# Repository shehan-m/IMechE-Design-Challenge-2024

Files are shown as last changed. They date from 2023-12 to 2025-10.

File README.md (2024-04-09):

# IMechE Design Challenge 2024

## Installation

OS: Raspberry Pi OS (Legacy, 32-bit) Lite

- **Step 1:** \
  To download code, it is necessary to have git installed:

```shell
sudo apt-get update && sudo apt-get install git -y
```

- **Step 2:** \
  Now install prerequisites for firmware:

```shell
sudo apt-get install python3-opencv && sudo apt-get install fswebcam
```

- **Step 3:** \
  Once these are installed, use the following command to clone the repo into the home directory:

```shell
cd ~ && git clone https://github.com/shehan-m/IMechE-Design-Challenge-2024/
```

## How to run code on startup

- **Step 1:** \
  Open the `rc.local` file using nano editor:

```shell
cd ~ && sudo nano /etc/rc.local
```

- **Step 2:** \
  Make bash script executable:

```shell
sudo chmod +x /IMechE-Design-Challenge-2024/Firmware/startup.sh
```

- **Step 3:** \
  Add the following commands above `exit 0`

```shell
sudo apt-get update && sudo apt-get install git -y
```

## Electronics

### Wiring Diagram
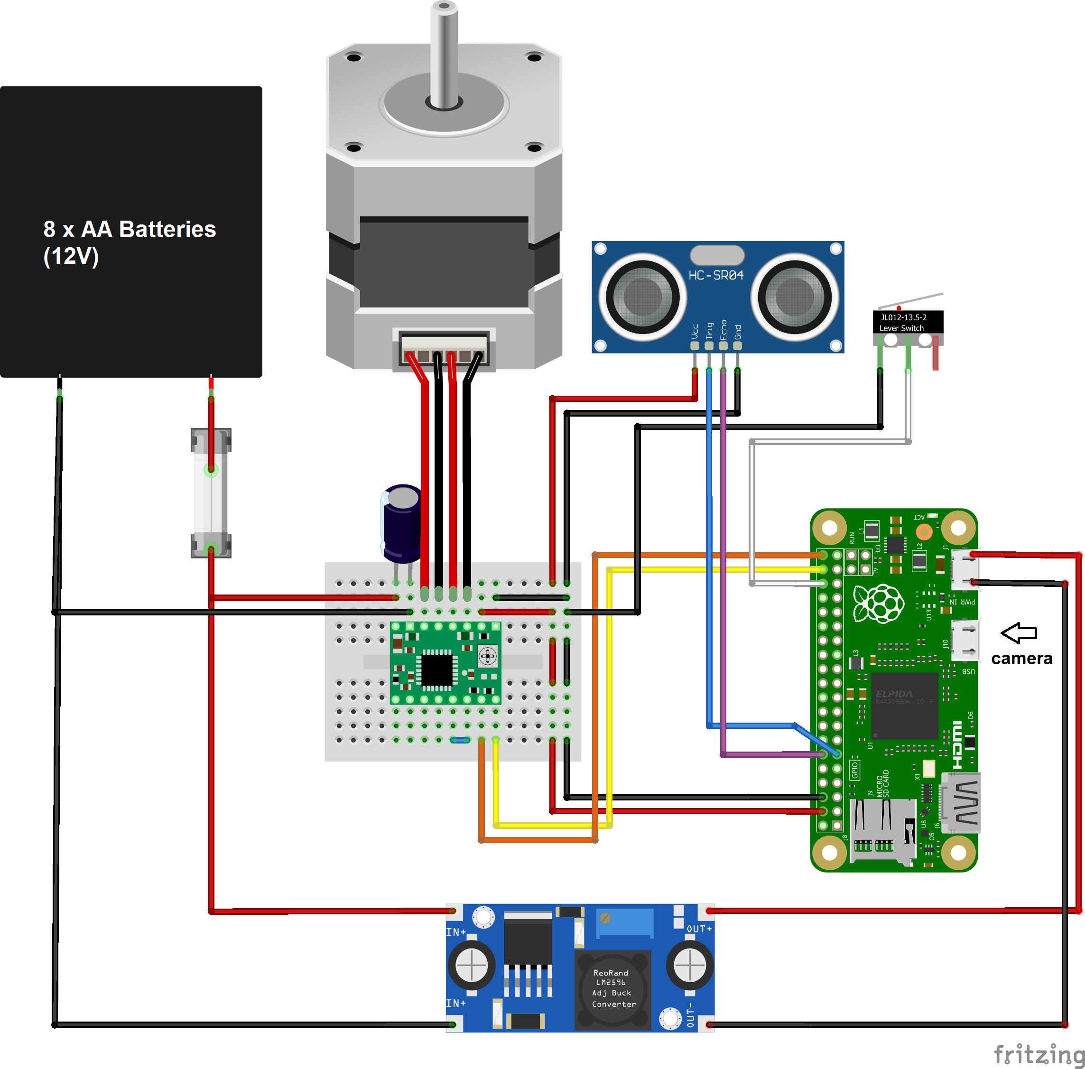
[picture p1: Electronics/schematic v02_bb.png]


### Limit switch

switch type: SPDT

#### This switch has three terminals:

- Common (COM): The common terminal
- Normally Open (NO): Connected to COM when the switch is pressed
- Normally Closed (NC): Connected to COM when the switch is not pressed

### Stepper driver current limiting

Vref = Imax * 8 * Rs

where, Imax is the current limit of the stepper motor, Rs is the resistance of the current sensing resistor (R5 on driver board)

In our case, Imax is 350 mA and Rs is 0.1 Ohms. Let's run the stepper motor at 60% of its rating. From this we get Vref:

Vref = (0.350 * 0.6) * 8 * 0.1 = 0.17 V

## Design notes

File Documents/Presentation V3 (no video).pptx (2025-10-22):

## IMechE Design Challenge 2024

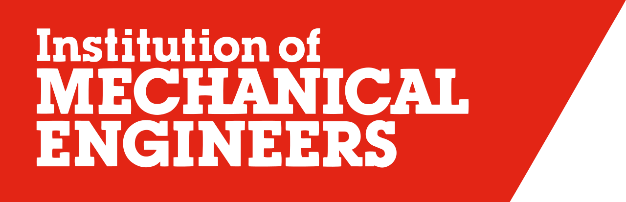
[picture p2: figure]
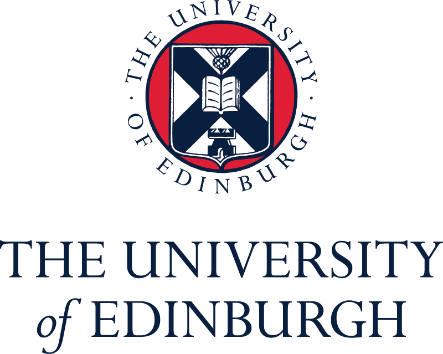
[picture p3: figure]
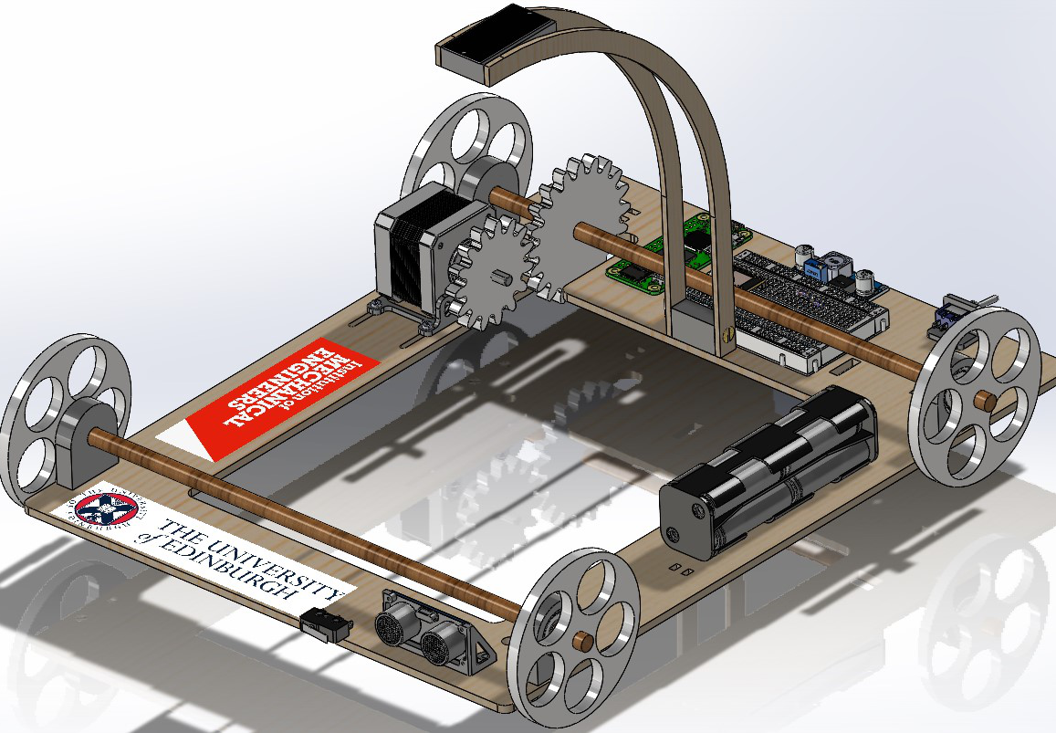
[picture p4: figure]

Gursager Singh
Shehan Medagedara
Harry Wang

## Challenge Overview

Advanced Category:
- Usage of Computer Vision
- Using motor and gear reduction for accurate movement

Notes: Went with Advanced category -> gave us the opportunity to use computer vision to detect the target, as well as use a motor in conjunction with gear reduction system to ensure accurate movement

## Vehicle Design

## Design Overview

NEMA 17 Stepper Motor

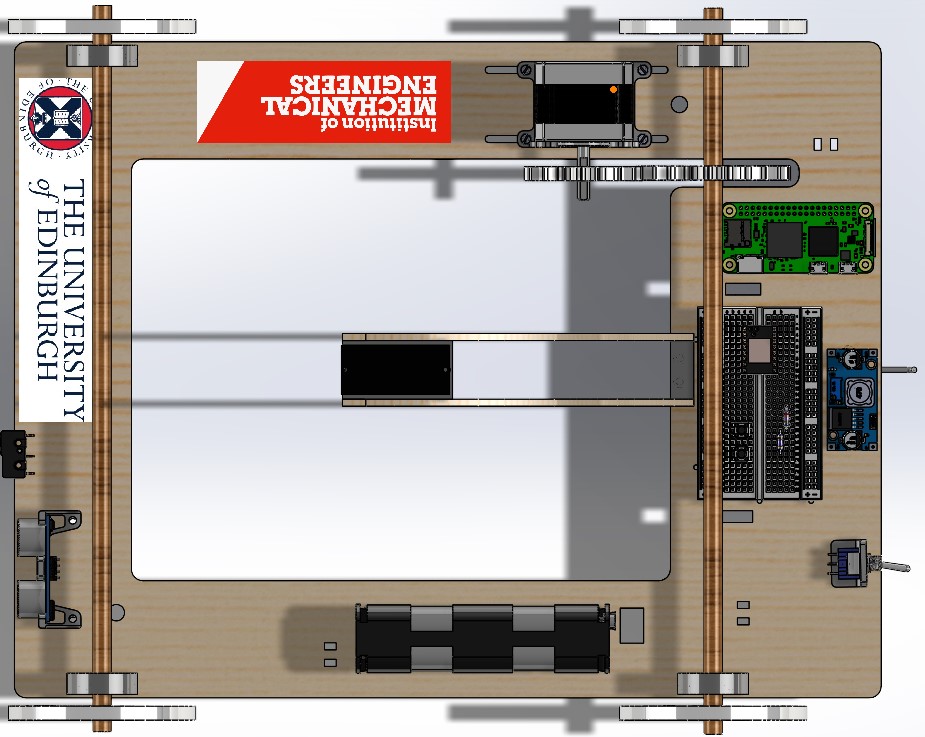
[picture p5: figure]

Wheel

Axle Holder + Ball bearings

Axle

Motor Gear

Raspberry Pi Zero 2 W

Breadboard

Output Gear

Limit Switch

TMC2208 V3 Stepper Driver

Buck Converter

Webcam

Ultrasonic Sensor (HC-SR04)

Battery Pack

On/Off Switch

## Chassis

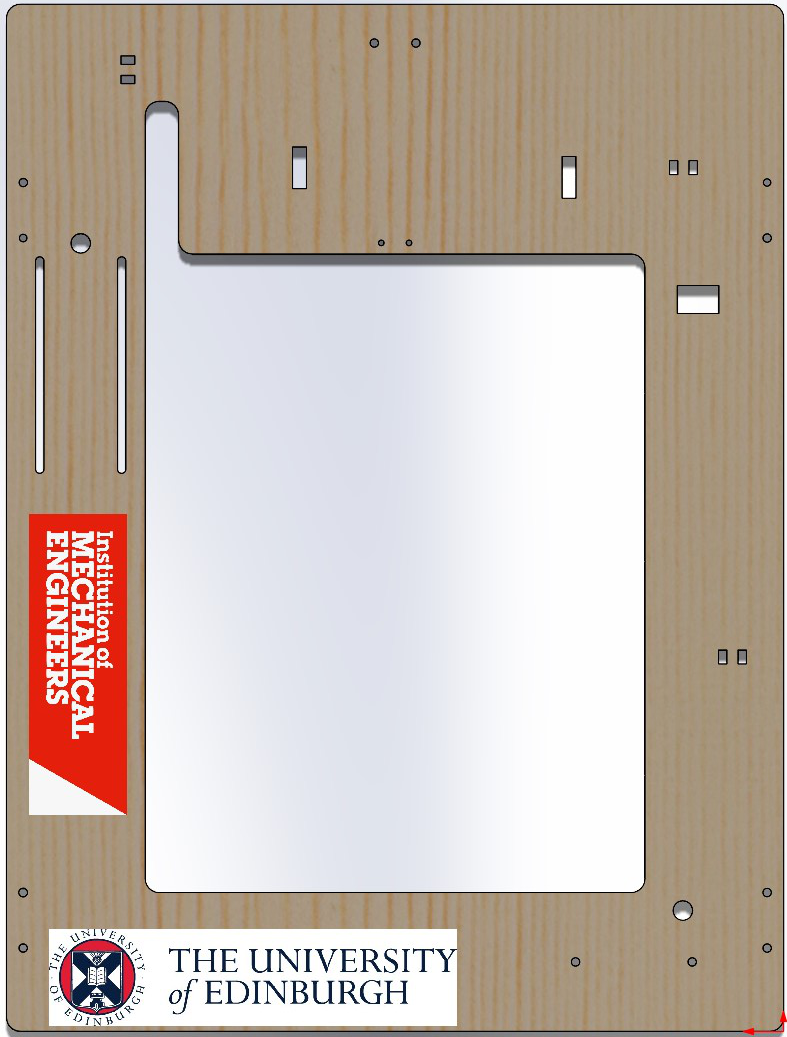
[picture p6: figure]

- 0.4mm MDF
- Target detection gap
- Drill holes to securing components
- Cable routing channels

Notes: 0.4mm MDF: perfect thickness and material to withstand weight and forces while staying relatively cheap
Large gap in centre for optimal target detection, system works best when target is directly underneath camera
Cable routing: ensures that the system looks neat, keeps cables out of the way. Dangling cables = hazard

## Powertrain

- NEMA 17 Motor
- Reduction gears at 4:3 reduction ratio
- Angular velocity of wheel = 0.75 of that of motor
- Allows stable movement

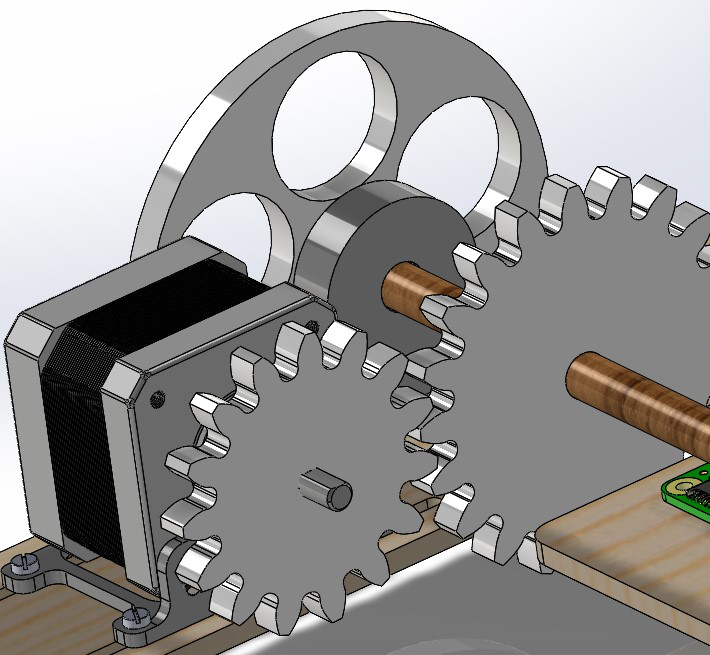
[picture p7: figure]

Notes: The NEMA 17 motor was chosen to deliver the power required

Motor needed to run at a certain angular velocity or else it will stutter. Reduction ratio allows the motor to run at higher speed while wheel travels slower and more accurately

## Target Detection Method

Initial idea: use a colour sensor with an Arduino
Problem: boundary between different colours could not be identified precisely
Solution: computer vision
= using an algorithm to detect circles from camera input

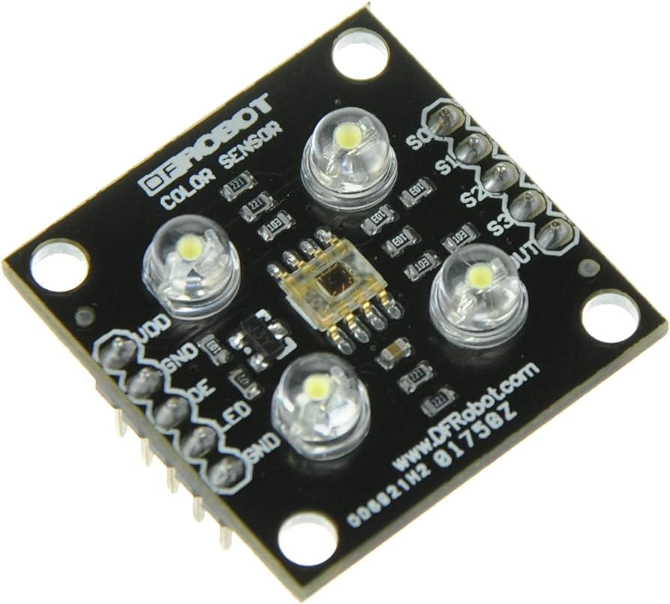
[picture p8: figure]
DFRobot SEN0101 TCS3200 Color Sensor/Color Detector : Amazon.ca: Tools & Home Improvement
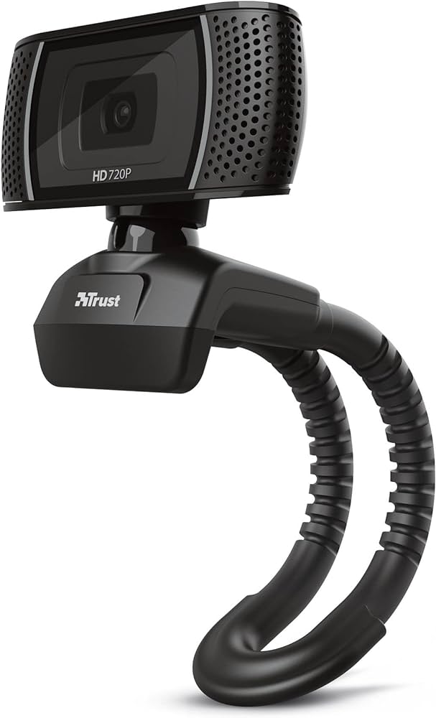
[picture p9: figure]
Trust Trino HD Webcam with Microphone, 1280x720, 30 FPS, Universal Stand, USB, Web Camera with Photo Button for Streaming, Video Calling, Skype, Teams, Zoom, PC, Computer, Laptop, Mac - Black : Amazon.co.uk:

## Circuit Diagram

Safety
- Power Switch
- Fuse
- Insulation on 12 V supply
Functionality
- Start button
- Reset button

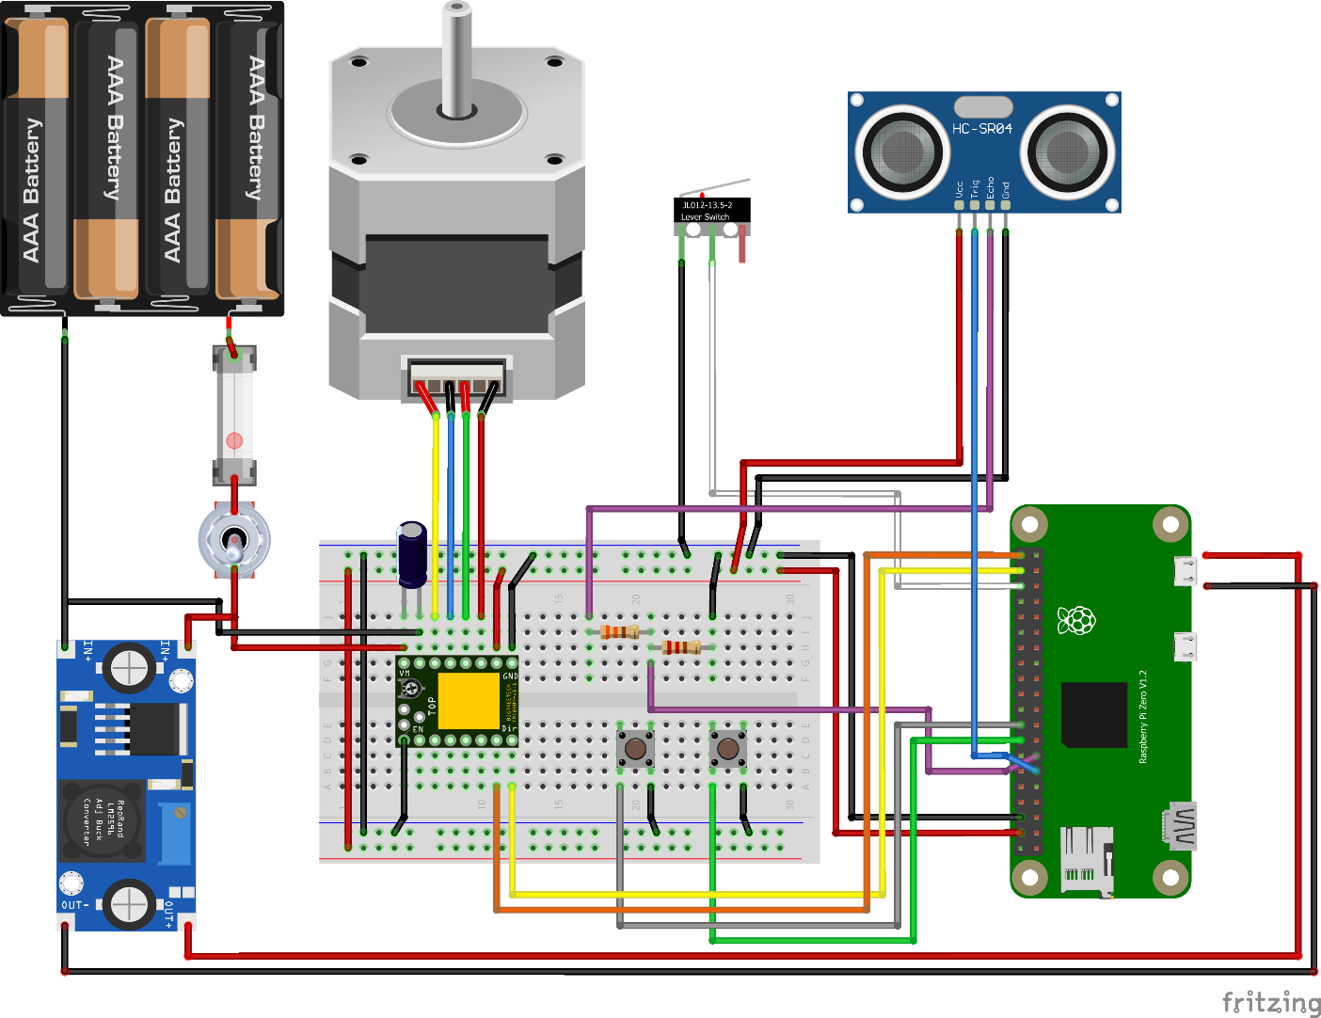
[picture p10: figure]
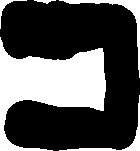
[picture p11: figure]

R2

12 V IN

R1

Camera In

5 V OUT

RESET Button

START Button

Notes: This circuit diagram outlines the essential components and connections for the device. Safety features include a power switch and a fuse to protect against electrical faults. A start and reset button can be used for easier control of the device.

## Power Distribution

Battery supply voltage:
- 12 V
Operating voltages:
- Stepper motor – 12 V
- Raspberry Pi – 5 V

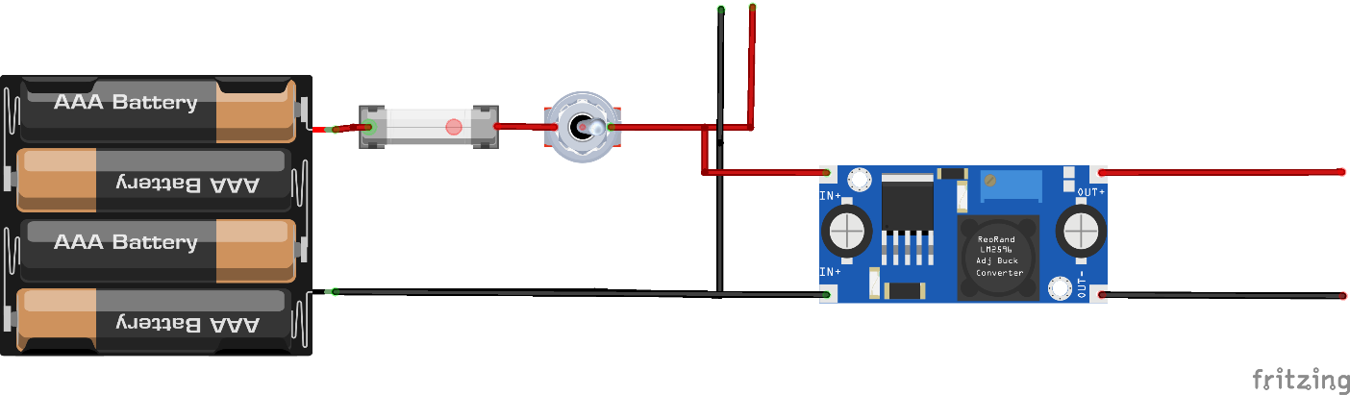
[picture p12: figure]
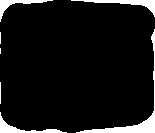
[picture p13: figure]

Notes: The whole system runs on a 12 V battery pack which has to power the Raspberry Pi and the stepper motor, both with different operating voltages. So, the supply voltage is split in parallel to the motor driver and to the buck converter. The buck converter steps down the battery voltage to 5 V which then supplies it to the Pi.

DO NOT READ:
- buck converter is a type of switch-mode power supply (SMPS) that changes voltage through duty cycle control.
- buck converter stabilises voltage - protect the Raspberry Pi against voltage fluctuations that could occur

## Calculating Vref

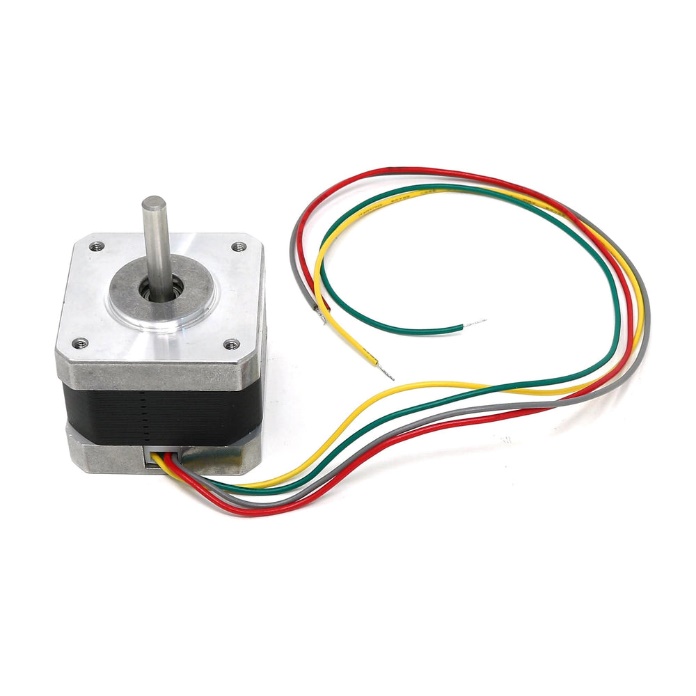
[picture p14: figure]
Stepper Motor - NEMA-17 size - 200 steps/rev, 12V 350mA - The Pi Hut

V_(ref) =I_(max) ∗8∗R_s
Where, I_(max) is the current limit of the stepper motor, R_s is the resistance of the current sensing resistor.
Motor Specification:
I_(max) = 350 mA
R_s = 0.1 Ω
V_(ref) =(0.350∗0.8)∗8∗0.1=0.22 V

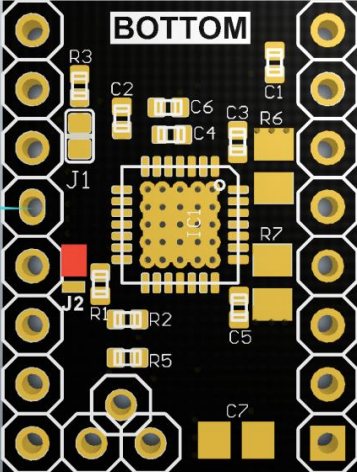
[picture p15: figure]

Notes:
The motor driver uses Vref to set the maximum amount of current that can flow through the motor coils. This needs to be calculate so not to damage the motor due to excessive current. For our case, Rs is the resistance of the R5 resistor on the driver board. From the motor specification we can get a Vref value of of 0.22 V. Also, to reduce heating in the motor, we’re operating it at 80% of its current limit.

## Protecting the Raspberry Pi

- General Purpose Input/Output (GPIO) pins on the Raspberry Pi operate at 3.3 V.
- Operating voltage of the ultrasonic sensor (HC-SR04) is 5 V.
- Thus, ultrasonic sensor input to Raspberry Pi must be lowered
V_(out) =(R1)/(R1+R2)∗V_(in) =330/(330+470) ∗5≈3.3 V
- Buck converter stabilises supply voltage.

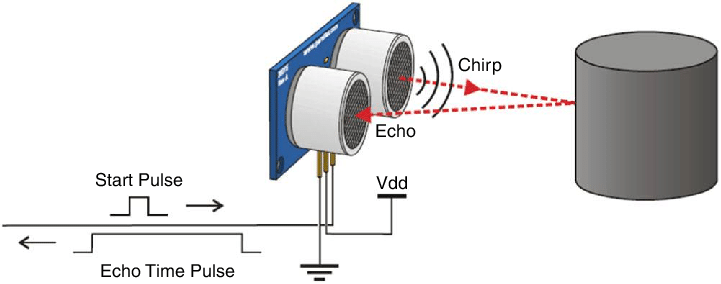
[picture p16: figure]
Working principle of ultrasonic sensor | Download Scientific Diagram

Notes: The GPIO pins on the Pi are designed to handle a maximum of 3.3 V. Exceeding this voltage can damage the Pi. This is a problem since the ultrasonic sensor operates at 5 V so, when the sensor sends an echo signal (indicating that it has detected an object) to the pi, the voltage level of this signal will be about 5 V. So, a potential divider is used to lower the echo signal voltage.

DO NOT READ: the echo signal is a series of HIGH & LOW (3.3V or 0 V) signals, so don’t have to save integrity of wave or anything like that

## Vehicle Operation

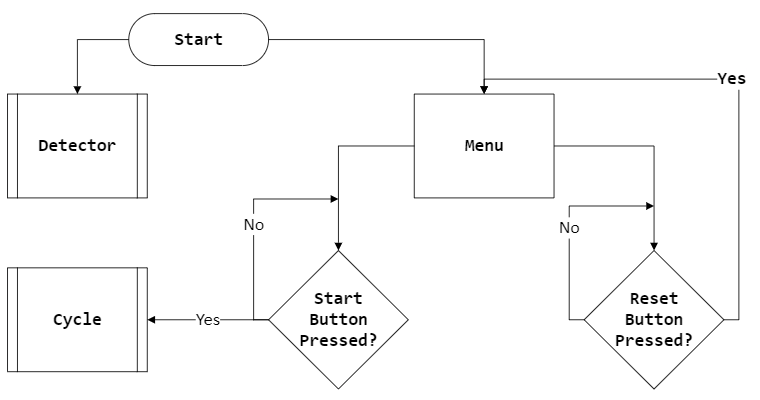
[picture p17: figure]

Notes: When the power switch is turned the the detector and a menu function starts. The menu continuously checks for button presses and starts the run/cycle if the start button is pressed, and reset the cycle if the reset is pressed. The detector starts at the same time as the menu because it takes time to boot up and vehicle doesn’t have to wait for that to happen.

## Vehicle Operation

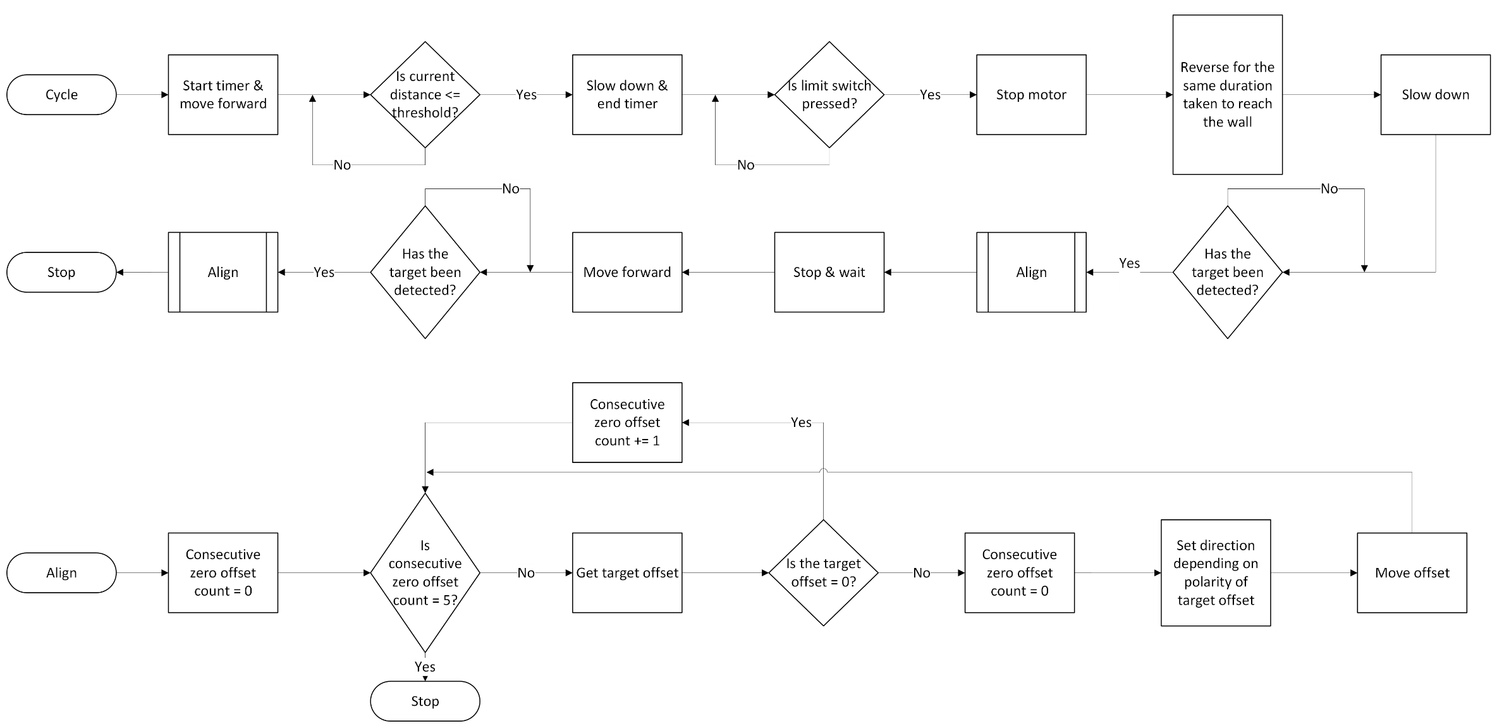
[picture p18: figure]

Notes:
Once the stat button has been pressed the vehicle moves towards the wall, continuously checking if the current distance to the wall is below a threshold value. If it is below the vehicle slows down and continues until the limit switch is pressed. Once this has been pressed the vehicle stops are reverse to the target and aligns itself. Once aligned, it waits and moves forward to the next target and aligns for a final time. The alignment process is very simple it moves motor by the offset given by the camera and does this until 5 offset readings return as 0 – meaning aligned.

Once the start button has been pressed the device begins to move forward & starts a timer. It continues to move forward until, the distance to the wall is less than a threshold value. Once at the threshold the device slows down, the timer is stopped and continues to move forward until the limit switch has been pressed. The motor stops & then reverses for the measured duration of time. After this time the device slows down and searches for the target. Once found it aligns itself & waits then moves forward to the second target and aligns again. The alignment process is very simple it moves the motor by offset given by the camera and does this until 5 offset readings return as 0 – meaning aligned.

## Detector – Computer Vision

Raw Input Video

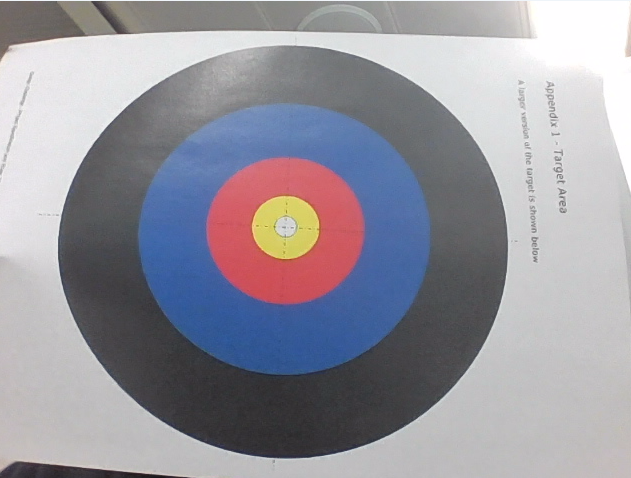
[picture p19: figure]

Colour Segmentation

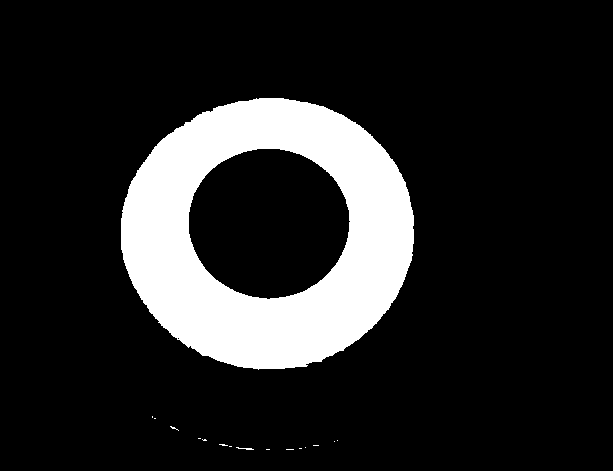
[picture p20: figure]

Mask Applied to Video

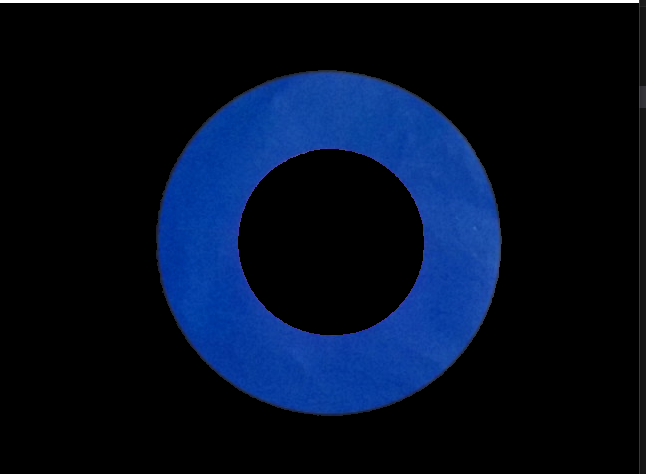
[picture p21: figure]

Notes: The input video feed is used to detect and isolate blue ring which can then be used to calculate the offset of its centre from the centre of the video.

To isolate the blue ring, a threshold is applied to select only the specified blue hues in the video. The white region represent where blue is detected.

This can then be used as a mask to get only the blue part of the input video.

## Detector – Computer Vision

Denoising

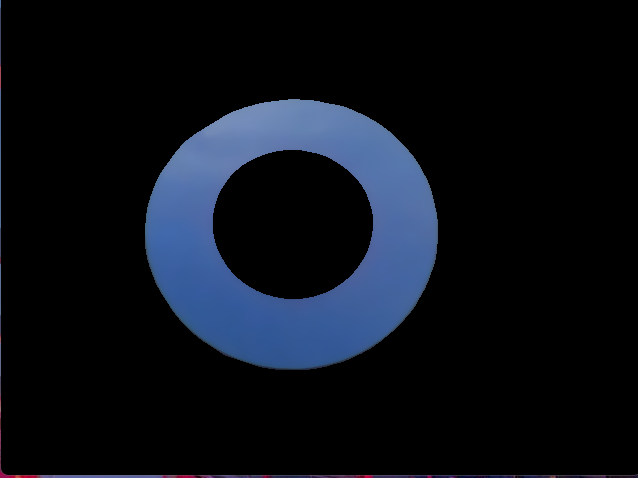
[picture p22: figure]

Greyscale Conversion

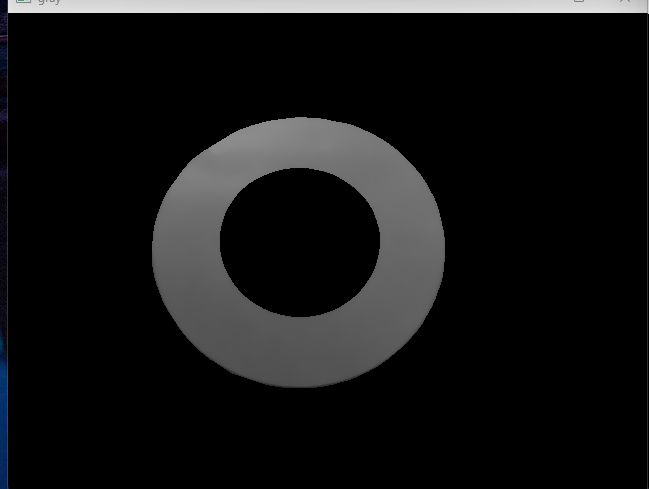
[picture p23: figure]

Contour Detection

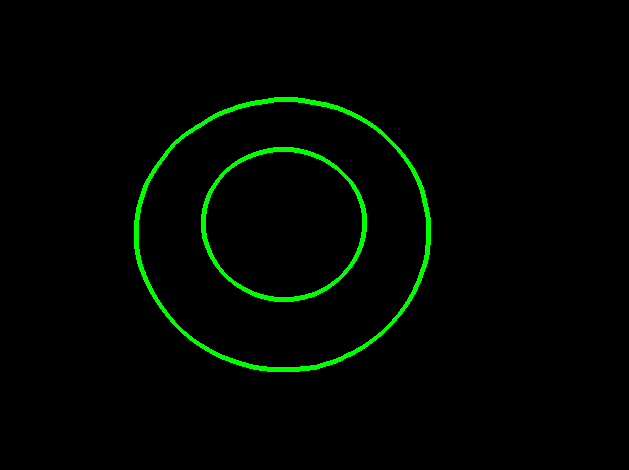
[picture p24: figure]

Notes: The produces a very noisy result which can affect the offset calculations. So, a median filter is applied to remove any noise.

Then converting the video to greyscale allows for easier and more accurate contour detection.

Finally, the contours are detected and are used to find the offset of the target from the centre of the video.

## Bill of Materials

## Overview

- Budget
- £80 excl. items less than 20p
- Total
- £79.25 excl. items less than 20p
- £82.96 incl. items more than 20p
- Remaining
- £0.75 from iMechE BoM

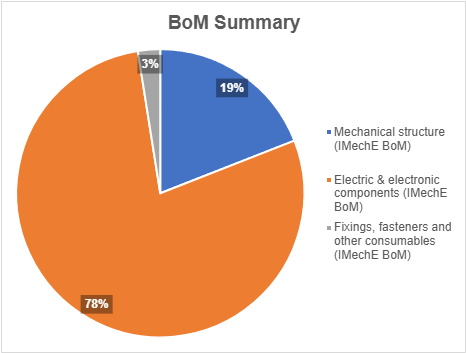
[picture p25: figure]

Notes: Note: do not simply just read off of the notes. Just say “here is the Bill of Materials overview” and state that we were under budget!

Pie chart shows for the iMechE BOM
Analyse from pie chart:
Focus on computer vision meant that more expenditure went towards electrical side
Mechanical components were quite cheap due to in-house facilities and smart usage of 3D printing and laser cutting

BOM shows well managed funding

## Thank you!

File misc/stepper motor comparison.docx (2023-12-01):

| NEMA 17 Stepper Motor | 28BYJ-48 Stepper Motor
Rated Voltage | 9-12 V | 5 V
Rated Current | 1.4 A
Step Angle | 0.9 degrees per step (micro stepping available) | 5.6 degrees per step
Torque | >= 0.127 Nm | >0.00343 Nm
Price | ~£10 | ~£8
Driver Included | No | Yes (ULN2003A)
Driver Price (if, not included) | ~£3-5 | N/A
Weight | 200 g | 33 g
Dimensions | 42.3 x 42.3 x 26.5 mm | 40 x 30 x 19 mm

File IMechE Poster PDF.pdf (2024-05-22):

## Target Detection

## Device Operation

## Bill of Materials

# IMechE Design Challenge 2024

Gursager Singh, Shehan Medagedara, Harry Wang

## Structure

Usage of iterative design and testing process
Laser cut MDF base structure for best support
Gap in centre of base to ensure best visual on target at a direct angle
Motor run through a 4:3 reduction gear system to ensure smooth and stable movement Cable-routing channels to ensure neat presentation

IMechE BoM Total: £73.07
Comprehensive Total: £77.00 Excess Funds: £6.93

Video feed is processed to highlight specific the colour of interest to act as a mask. In this case, blue. The mask is applied to the input video.

Noise is removed from the masked video by applying a median filter. Then, converted to greyscale for easier contour detection. The Centre of the target is determined from the centre of largest contour.

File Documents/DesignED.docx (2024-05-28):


DesignED

Gursager Singh

Shehan Medagedara

Harry Wang

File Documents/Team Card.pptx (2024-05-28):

## DesignED


Gursager Singh Hardeep Singh
Shehan Medagedara
Harry Wang

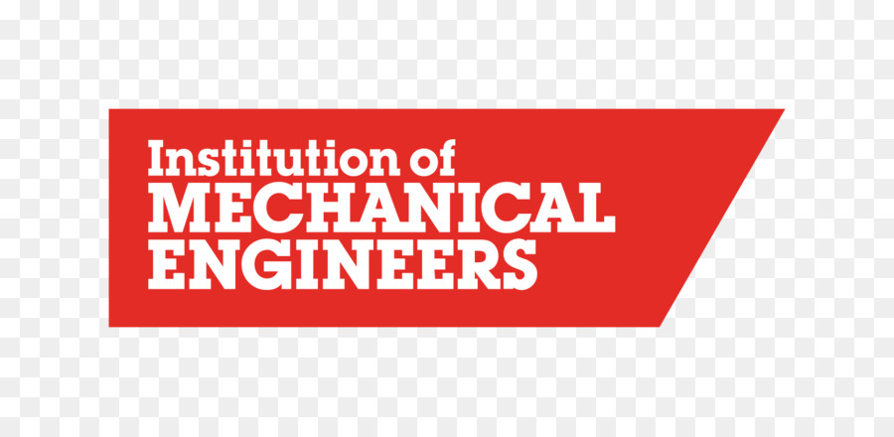
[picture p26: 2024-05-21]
Pictures/kisspng-institution-of-mechanical-engineers-mechanical-eng-mechanical-engine.jpg

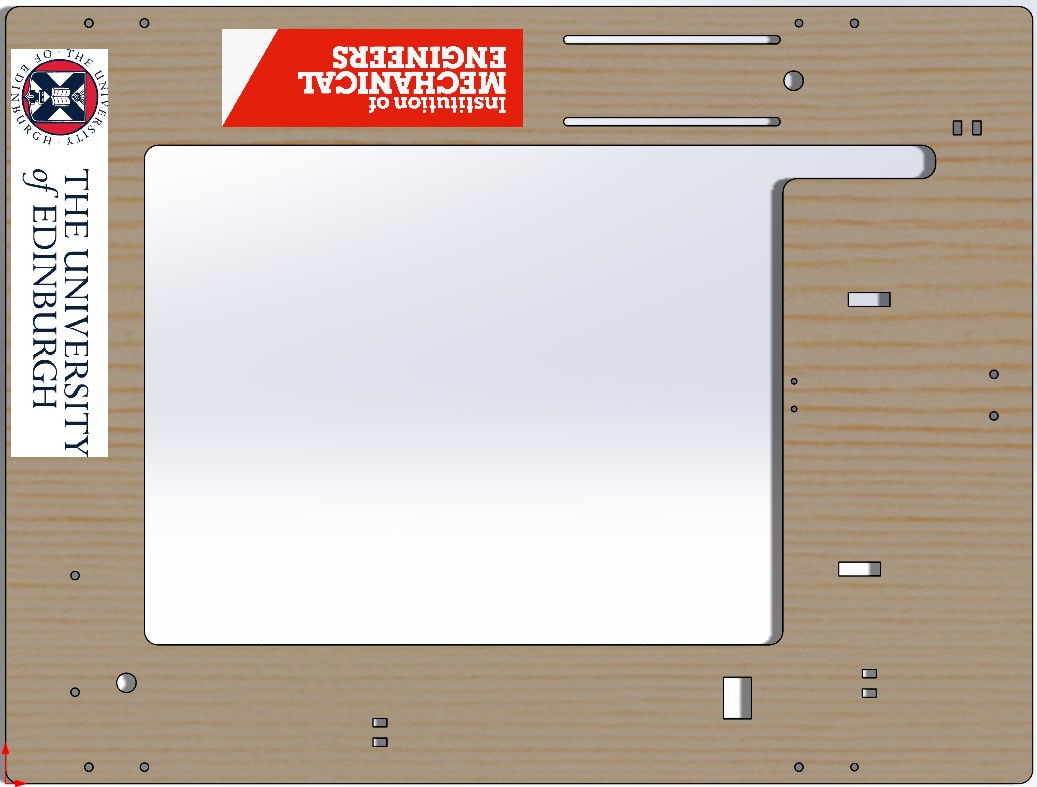
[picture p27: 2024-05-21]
Pictures/Chassis.jpg

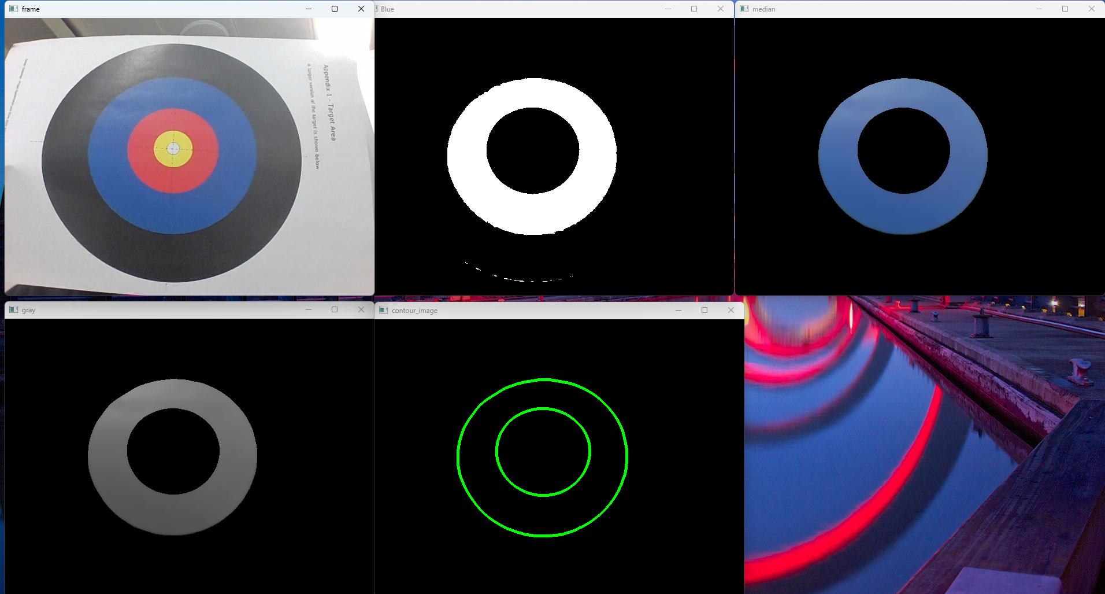
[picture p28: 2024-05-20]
Electronics/Screenshot 2024-05-20 135401.png

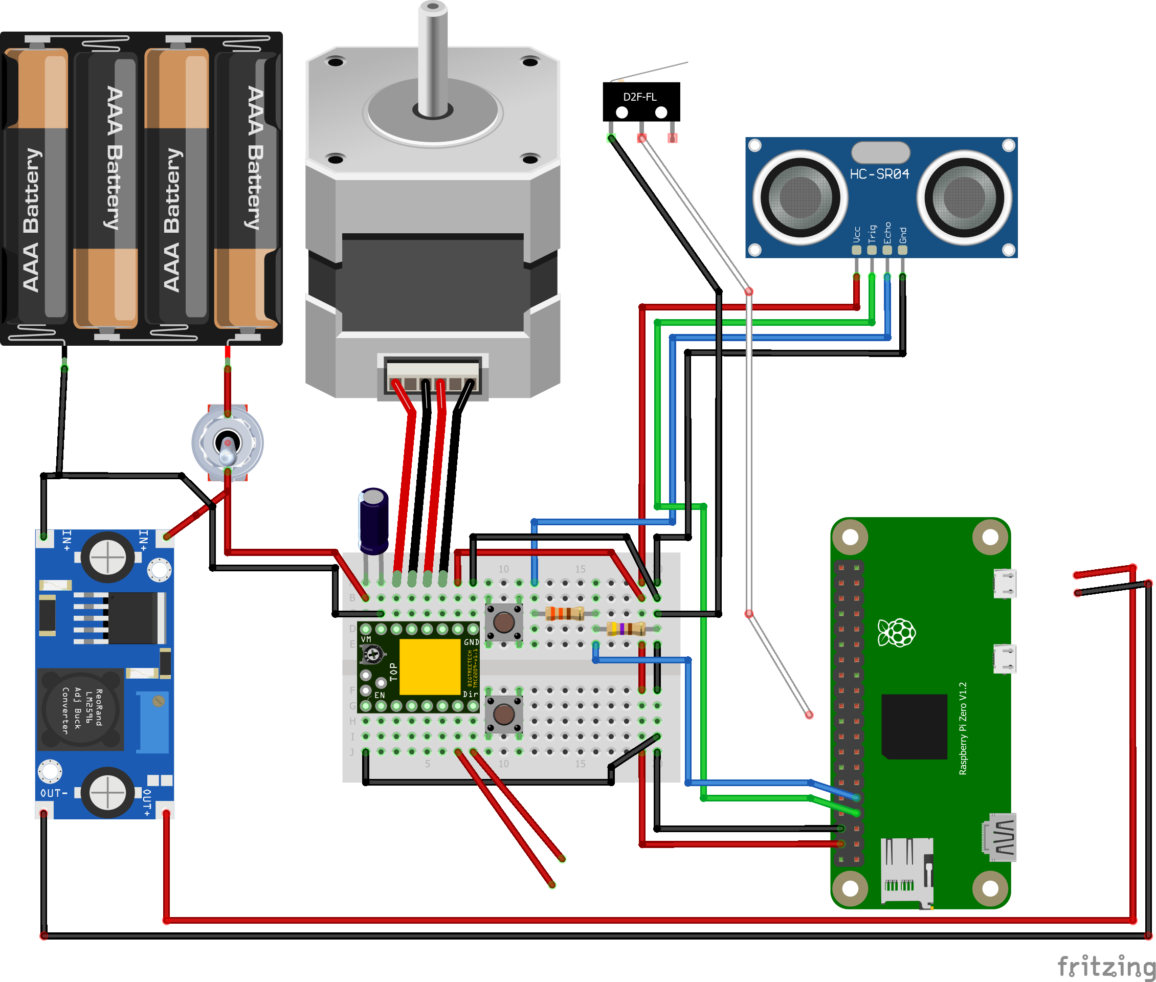
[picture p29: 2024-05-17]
Electronics/circuit diagram v03_bb.png

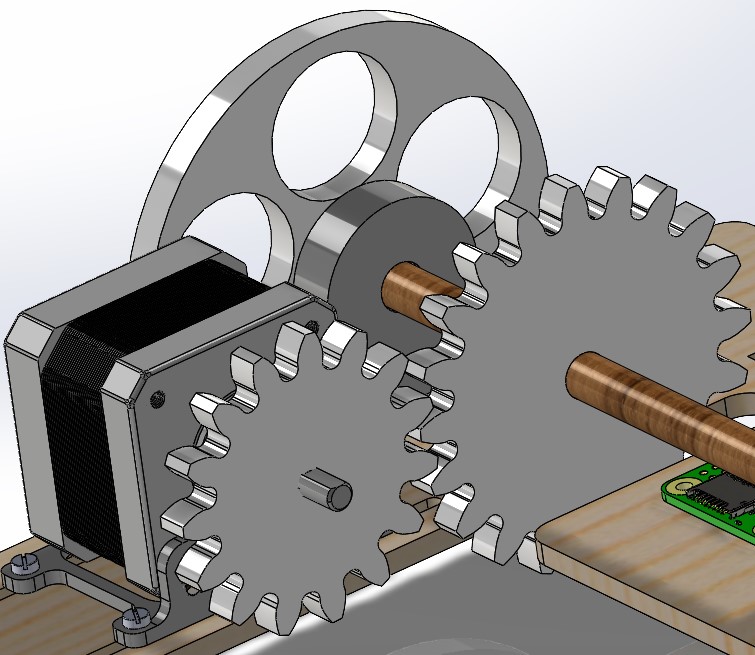
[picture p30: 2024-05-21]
Pictures/Powertrain.jpg

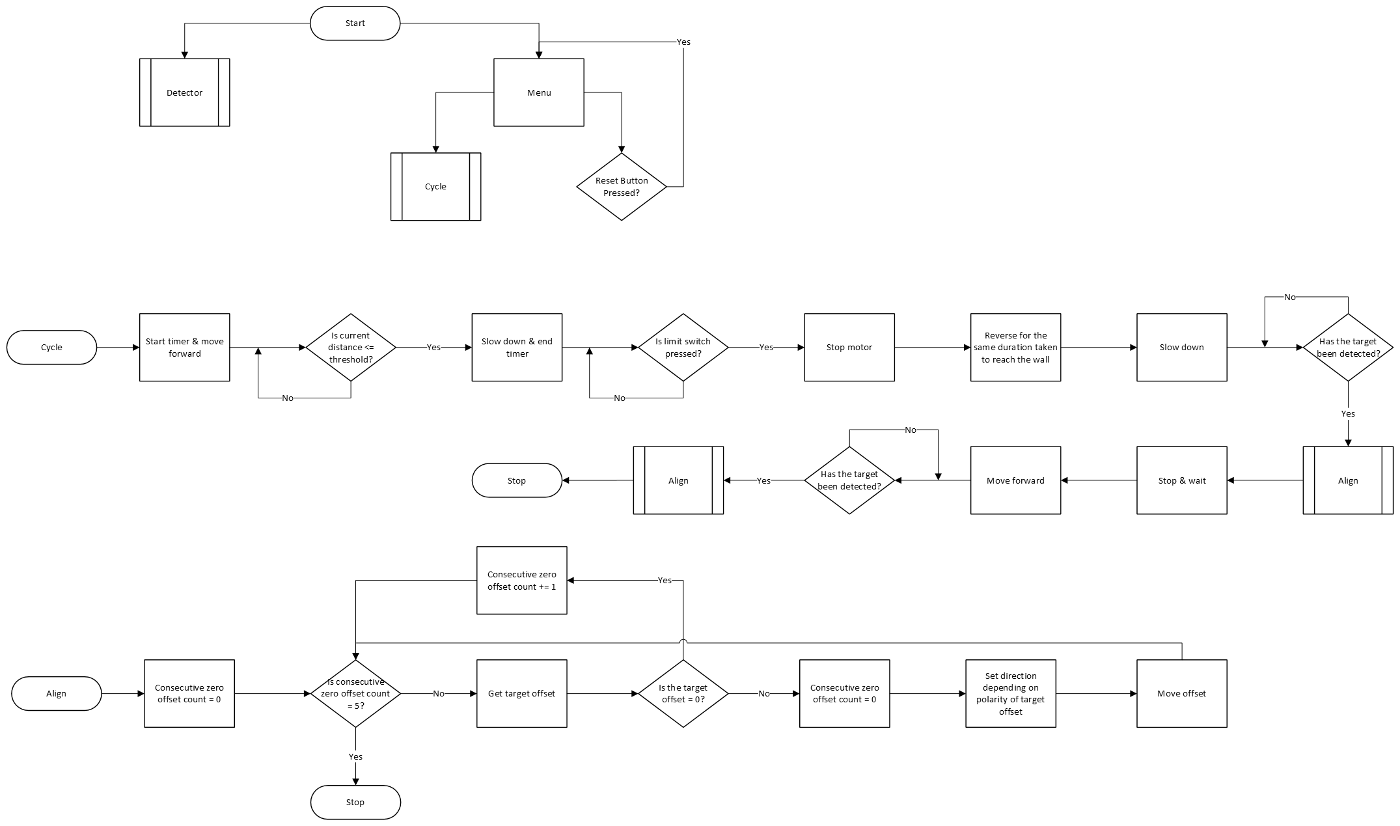
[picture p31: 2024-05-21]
Pictures/Flowchart.png

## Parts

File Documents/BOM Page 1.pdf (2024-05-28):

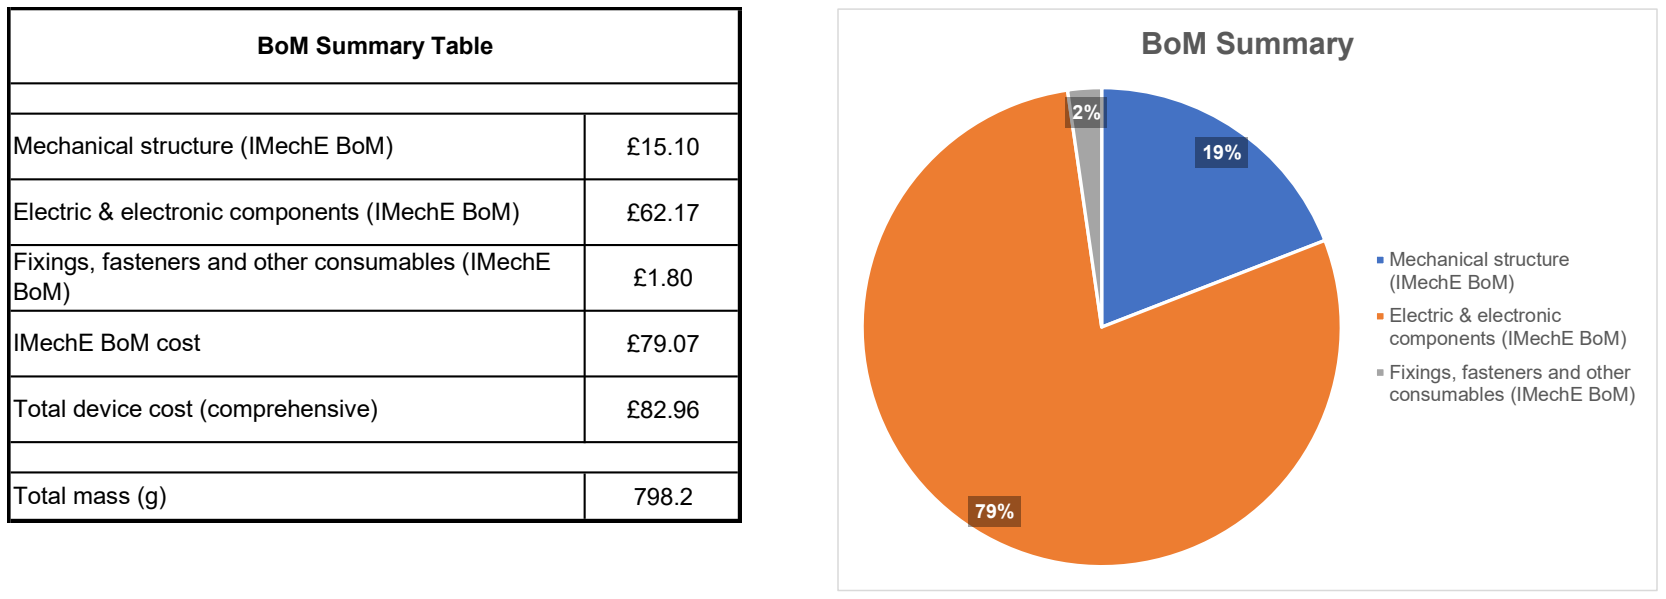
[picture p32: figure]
Mechanical structure (IMechE BoM); IMechE BoM cost; Total device cost (comprehensive); Total mass (g); BoM Summary Table; BoM Summary; Electric & electronic components (IMechE BoM); Fixings, fasteners and other consumables (IMechE BoM)

Electric & electronic components (IMechE BoM) | £62.17
Fixings, fasteners and other consumables (IMechE BoM) | £1.80

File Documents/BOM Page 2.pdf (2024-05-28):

Device Area | BoM Item Line | Part Number | Design Iteration | Part Name | Quantity (units, g, mm, mm2) | Unit Cost (£/unit; £/g; £/mm - VAT inc.) | Total Cost ( £ - VAT inc.) | IMechE BoM Cost ( £ -VAT inc.) | | Material | (kg/m3) Density | Mass (g) | Total Mass (g) | Manufacturing Technique / Purchased Item | Supplier | Hyperlink | Invoices (see notes below)
| 1 | M0001 | 1 | IMechE Standard datum pointer | 1 | £0.14 | £0.14 | £0.00 | | Brass | 8350 | 1 | 1 | COtS | RS Components | Link | Invoice 4
| 2 | M0002 | 2 | 8 mm Rod | 620 | 2.60E-04 | £0.16 | £0.00 | | Hard Wood | 650 | 19.6 | 19.6 | Cut to size | WF Education Group | Link | Invoice 2
| | 3 | M0003 | 1 | 608zz Bearings | 4 | £0.30 | £1.20 | £1.20 | | - | N/A | 10 | 40 | COtS | Amazon UK | Link | Invoice 1
| | 4 | M0004 | 1 | Ultrasonic sensor holder | 1.62 | £0.10 | £0.16 | £0.00 | | PLA+ | 1250 | 1.62 | 1.62 | 3D Printed | - | - | -
| | 5 | M0005 | 2 | Motor mount | 2.46 | £0.10 | £0.25 | £0.25 | | PLA+ | 1250 | 2.46 | 2.46 | 3D Printed | - | - | -
| | 6 | M0006 | 6 | Chassis | 60700 | 4.06E-06 | £0.25 | £0.25 | | MDF | 360 | 87 | 87 | Laser Cut | Hobarts | Link | -
| | 7 | M0007 | 4 | Datum holder | 1.6 | £0.10 | £0.16 | £0.00 | | PLA | 800 | 1.6 | 1.6 | 3D Printed | - | - | -
| | 8 | M0008 | 4 | Drive gear | 1500 | 6.21E-04 | £0.93 | £0.93 | | Perspex | 1250 | 11.5 | 11.5 | Laser Cut | Hobarts | Link | -
| | 9 | M0009 | 4 | Output gear | 2700 | 6.21E-04 | £1.68 | £1.68 | | Perspex | 1250 | 20.5 | 20.5 | Laser Cut | Hobarts | Link | -
| | 10 | M0010 | 3 | Wheel | 2500 | 6.21E-04 | £1.55 | £1.55 | | Perspex | 1250 | 18.9 | 18.9 | Laser Cut | Hobarts | Link | -
| | 11 | M0011 | 1 | Axle holder | 15.2 | £0.10 | £1.52 | £1.52 | | PLA | 1250 | 5 | 20 | 3D Printed | - | - | -
| | 12 | M0012 | 1 | Bottom bracket | 3 | £0.10 | £0.30 | £0.30 | | PLA | 1250 | 3 | 3 | 3D Printed | - | - | -
| | 13 | M0013 | 2 | Camera holder | 6 | £0.10 | £0.60 | £0.60 | | PLA | 1250 | 6 | 6 | 3D Printed | - | - | -
| | 14 | M0014 | 2 | Camera arm | 5800 | 4.06E-06 | £0.02 | £0.00 | | MDF | 360 | 7 | 14 | Laser Cut | Hobarts | Link | -
| | 15 | M0015 | 1 | Stiffener | 11000 | 6.21E-04 | £6.83 | £6.83 | | Perspex | 1250 | 82.5 | 82.5 | Laser Cut | Hobarts | Link | -
| | Mechanical IMechE BoM - Partial (£) | | | | | | | £15.10
16 | E0001 | 2 | Raspberry Pi Zero 2 W | 1 | £14.88 | £14.88 | £14.88 | - | - | 14 | 14 | COtS | CPC Farnell | Link | Invoice 11
17 | E0002 | 2 | Webcam | 1 | £9.99 | £9.99 | £9.99 | - | - | 47 | 47 | COtS | Argos | Link | Invoice 3
18 | E0003 | 1 | NEMA 17 | 1 | £12.00 | £12.00 | £12.00 | - | - | 64 | 64 | COtS | RS components | Link | Invoice 7
19 | E0004 | 2 | TMC2208 Driver | 1 | £5.25 | £5.25 | £5.25 | - | - | 3 | 3 | COtS | 3DJake | Link | Invoice 12
20 | E0005 | 1 | MicroSD card | 1 | £5.39 | £5.39 | £5.39 | - | - | 0.25 | 0.25 | COtS | CPC Farnell | Link | Invoice 6
21 | E0006 | 2 | Microswitch | 1 | £0.35 | £0.35 | £0.35 | - | - | 3 | 3 | COtS | Amazon UK | Link | Invoice 8
22 | E0007 | 1 | 8x Battery holder | 1 | £0.98 | £0.98 | £0.98 | - | - | 16 | 16 | COtS | CPC Farnell | Link | Invoice 6
23 | E0008 | 1 | Snap-on battery connector | 1 | £0.23 | £0.23 | £0.23 | - | - | 20 | 20 | COtS | CPC Farnell | Link | Invoice 6
24 | E0009 | 1 | Micro USB adapter | 1 | £0.77 | £0.77 | £0.77 | - | - | 13 | 13 | COtS | CPC Farnell | Link | Invoice 6
25 | E0010 | 1 | Micro USB Cable | 1 | £0.96 | £0.96 | £0.96 | - | - | 8 | 8 | Cut to size | RS components | Link | Invoice 4
26 | E0011 | 1 | DC-DC buck converter | 1 | £1.40 | £1.40 | £1.40 | - | - | 12 | 12 | COtS | Amazon UK | Link | Invoice 1
27 | E0012 | 1 | Header pin, 1 row, 20 way | 2 | £0.10 | £0.20 | £0.00 | - | - | 0.6 | 1.2 | COtS | CPC Farnell | Link | Invoice 5
28 | E0013 | 2 | SPDT Switch | 1 | £0.35 | £0.35 | £0.35 | - | - | 5 | 5 | COtS | Amazon UK | Link | Invoice 9
29 | E0014 | 1 | AA Battery | 8 | £0.70 | £5.60 | £5.60 | - | - | 24 | 192 | COtS | Amazon UK | Link | -
30 | E0015 | 1 | 100uF capacitor | 1 | £0.12 | £0.12 | £0.00 | - | - | 1 | 1 | COtS | CPC Farnell | Link | Invoice 10
31 | E0016 | 1 | Breadboard | 1 | £0.90 | £0.90 | £0.90 | - | - | 33 | 33 | COtS | CPC Farnell | Link | Invoice 10
32 | E0017 | 1 | 6.3A fuse | 1 | £0.14 | £0.14 | £0.00 | - | - | 0.81 | 0.81 | COtS | CPC Farnell | Link | Invoice 10
33 | E0018 | 1 | Buttons | 2 | £0.04 | £0.08 | £0.00 | | | 0.3 | 0.6 | COtS | Amazon UK | Link | -
34 | E0019 | 1 | In-line fuse holder | 1 | £0.60 | £0.60 | £0.60 | - | - | 4.5 | 4.5 | COtS | CPC Farnell | Link | Invoice 10
35 | E0020 | 1 | Jumper wire | 26 | £0.06 | £1.51 | £0.00 | - | - | 0.66 | 17.16 | COtS | Amazon UK | Link | Invoice 10
36 | E0021 | 1 | Ultrasonic distance sensor | 1 | £2.52 | £2.52 | £2.52 | - | - | 8 | 8 | COtS | RS components | Link | Invoice 4
Electronics IMechE BoM - Partial (£) | | | | | | | £62.17
37 | CF0001 | 1 | Heatshrink | 10 | £0.02 | £0.19 | £0.00 | EVA | - | 5 | 5 | Cut to size | Amazon UK | Link | -
38 | CF0002 | 1 | Hot glue | 0.8 | £0.78 | £0.62 | £0.62 | - | - | 10 | 10 | CotS | Screwfix | Link | -
39 | CF0003 | 1 | Lead-free solder | 2 | £0.17 | £0.34 | £0.00 | - | - | 2 | 2 | Cut to size | RS Components | Link | -
40 | CF0004 | 1 | Stranded-core wire | 800 | 2.37E-04 | £0.19 | £0.00 | - | - | 8 | 8 | Cut to size | Pi Hut UK | Link | -
41 | CF0005 | 1 | Solid-core wire | 100 | 2.63E-04 | £0.03 | £0.00 | - | - | 8 | 8 | Cut to size | Pi Hut UK | Link | -
42 | CF0006 | 1 | Super glue | 1 | £0.72 | £0.72 | £0.72 | - | - | 1 | 1 | CotS | Amazon UK | Link | -
43 | CF0007 | 2 | Velcro tape | 60 | 2.60E-03 | £0.16 | £0.16 | - | - | 8 | 8 | Cut to size | Amazon UK | Link | -
44 | CF0009 | 1 | M3x6 | 2 | £0.01 | £0.03 | £0.00 | Stainless
| | | | | | | | Steel | 8000 | 0.36 | 0.72 | COtS | Amazon UK | Link | Invoice 8
45 | CF0010 | 1 | M3 nut | 2 | £0.01 | £0.03 | £0.00 | Stainless
| | | | | | | | Steel | 8000 | 0.4 | 0.8 | COtS | Amazon UK | Link | Invoice 8
46 | CF0011 | 1 | M3 nylock nut | 2 | £0.03 | £0.03 | £0.00 | Stainless
| | | | | | | | Steel | - | 0.4 | 0.8 | CotS | BoltWorld | Link | -
47 | CF0012 | 1 | M2 nut | 2 | £0.01 | £0.03 | £0.00 | Stainless
| | | | | | | | Steel | 8000 | 0.1 | 0.2 | COtS | Amazon UK | Link | Invoice 8
48 | CF0013 | 1 | M3x10 | 16 | £0.01 | £0.21 | £0.00 | Stainless
| | | | | | | | Steel | 8000 | 0.5 | 8 | COtS | Amazon UK | Link | Invoice 8
49 | CF0014 | 1 | M2.5x12 | 6 | £0.01 | £0.08 | £0.00 | Stainless
| | | | | | | | Steel | 8000 | 0.4 | 2.4 | COtS | Amazon UK | Link | Invoice 8
50 | CF0015 | 1 | M2x10 | 2 | £0.01 | £0.03 | £0.00 | Stainless
| | | | | | | | Steel | 8000 | 0.22 | 0.44 | COtS | Amazon UK | Link | Invoice 8
51 | CF0016 | 1 | Electrical tape | 400 | 3.33E-05 | £0.01 | £0.00 | PVC | - | 3 | 3 | Cut to size | Screwfix | Link | -
52 | CF0017 | 1 | Printing + Glue Stick | 1 | £ | 0.30 | £0.30 | £0.30 | Paper | - | - | - | Printed | in-house
| | | | | | | £1.80 | | | | 798.2

Notes:

Access
invoices here | Back up link:
https://uoe-my.sharepoint.com/:f:/g/personal/s2289738_ed_ac_uk/EtWzKMgK9zBFi7NRyLfgglQBb7IdocdMV8jteqt58a28lA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

Unit costs that are too small are denoted in scientific form (ie 4.06E-6) and are still in the unit £

Quantity is in units, except for those which are laser cut (mm2), those which are 3D printed (g), or tape/cut (mm) Mechanical Electronics

Bill of Materials Fixings, Fasteners, and other consumeables

Consumables IMechE BoM - Partial (£) | Total Mass (g)

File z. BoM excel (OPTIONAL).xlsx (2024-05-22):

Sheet: Summary
BoM Summary Table
Mechanical structure (IMechE BoM) | £9.80
Electric & electronic components (IMechE BoM) | £62.17
Fixings, fasteners and other consumables (IMechE BoM) | £1.11
IMechE BoM cost | £73.07
Total device cost (comprehensive) | £77.00
Total mass (g) | 723.28

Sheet: Bill of Materials
Bill of Materials
Device Area | BoM Item Line | Part Number | Design Iteration | Part Name | Quantity (units, g, mm, mm2) | Unit Cost (£/unit; £/g; £/mm - VAT inc.) | Total Cost ( £ - VAT inc.) | IMechE BoM Cost ( £ - VAT inc.) | Material | Density (kg/m3) | Mass (g) | Total Mass (g) | Manufacturing Technique / Purchased Item | Supplier | Hyperlink | Invoices (see notes below)
Mechanical | 1 | M0001 | 1 | IMechE Standard datum pointer | 1 | £0.14 | £0.14 | £0.00 | Brass | 8350 | 1 | 1 | COtS | RS Components | Link (https://uk.rs-online.com/web/p/hooks/3974954) | Invoice 4
 | 2 | M0002 | 2 | 8 mm Rod | 600 | 0.00026 | £0.16 | £0.00 | Hard Wood | 650 | 19.6 | 19.6 | Cut to size | WF Education Group | Link (https://shop.wf-education.com/dnt/950-694.html) | Invoice 2
 | 3 | M0003 | 1 | 608zz Bearings | 4 | £0.30 | £1.20 | £1.20 | - | N/A | 10 | 40 | COtS | Amazon UK | Link (https://www.amazon.co.uk/dp/B09PVDDBWF?psc=1&ref=ppx_yo2ov_dt_b_product_details) | Invoice 1
 | 4 | M0004 | 1 | Ultrasonic sensor holder | 1.62 | £0.10 | £0.16 | £0.00 | PLA+ | 1250 | 1.62 | 1.62 | 3D Printed | - | - | -
 | 5 | M0005 | 2 | Motor mount | 2.46 | £0.10 | £0.25 | £0.25 | PLA+ | 1250 | 2.46 | 2.46 | 3D Printed | - | - | -
 | 6 | M0006 | 6 | Chassis | 60684 | 4.056e-06 | £0.25 | £0.25 | MDF | 360 | 87 | 87 | Laser Cut | Hobarts | Link (https://hobarts.com/products/pack-13-4-0mm-laser-grade-mdf-size-600x300mm-x50-sheets?variant=44274900435181) | -
 | 7 | M0007 | 2 | Datum holder | 6 | £0.10 | £0.60 | £0.60 | PLA | 800 | 6 | 6 | 3D Printed | - | - | -
 | 8 | M0008 | 4 | Drive gear | 1542 | 0.000621 | £0.96 | £0.96 | Perspex | 1250 | 11.5 | 11.5 | Laser Cut | Hobarts | Link (https://hobarts.com/products/clear-cast-perspex-acrylic-large?variant=43956358775021) | -
 | 9 | M0009 | 4 | Output gear | 2734 | 0.000621 | £1.70 | £1.70 | Perspex | 1250 | 20.5 | 20.5 | Laser Cut | Hobarts | Link (https://hobarts.com/products/clear-cast-perspex-acrylic-large?variant=43956358775021) | -
 | 10 | M0010 | 3 | Wheel | 2522 | 0.000621 | £1.57 | £1.57 | Perspex | 1250 | 18.9 | 18.9 | Laser Cut | Hobarts | Link (https://hobarts.com/products/clear-cast-perspex-acrylic-large?variant=43956358775021) | -
 | 11 | M0011 | 1 | Axle holder | 20 | £0.10 | £2.00 | £2.00 | PLA | 1250 | 5 | 20 | 3D Printed | - | - | -
 | 12 | M0012 | 1 | Bottom bracket | 3 | £0.10 | £0.30 | £0.30 | PLA | 1250 | 3 | 3 | 3D Printed | - | - | -
 | 13 | M0013 | 2 | Camera holder | 6 | £0.10 | £0.60 | £0.60 | PLA | 1250 | 6 | 6 | 3D Printed | - | - | -
 | 14 | M0014 | 2 | Camera arm | 5840 | 4.056e-06 | £0.02 | £0.00 | MDF | 360 | 7 | 14 | Laser Cut | Hobarts | Link (https://hobarts.com/products/pack-13-4-0mm-laser-grade-mdf-size-600x300mm-x50-sheets?variant=44274900435181) | -
 | 15 | M0015 | 1 | RPi Spacer | 0.96 | £0.10 | £0.38 | £0.38 | PLA | 1250 | 0.96 | 3.84 | 3D Printed | - | - | -
 | Mechanical IMechE BoM - Partial (£) |  |  |  |  |  |  | £9.80
Electronics | 16 | E0001 | 2 | Raspberry Pi Zero 2 W | 1 | £14.88 | £14.88 | £14.88 | - | - | 14 | 14 | COtS | CPC Farnell | Link (https://cpc.farnell.com/raspberry-pi/rpi-zero-w-v2/raspberry-pi-zero-w-v2/dp/SC19061?st=raspberry%20pi%20zero) | Invoice 11
 | 17 | E0002 | 2 | Webcam | 1 | £9.99 | £9.99 | £9.99 | - | - | 47 | 47 | COtS | Argos | Link (https://www.argos.co.uk/product/8739816) | Invoice 3
 | 18 | E0003 | 1 | NEMA 17 | 1 | £12.00 | £12.00 | £12.00 | - | - | 64 | 64 | COtS | RS components | Link (https://uk.rs-online.com/web/p/power-motor-robotics-development-tools/1845109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) | Invoice 7
 | 19 | E0004 | 2 | TMC2208 Driver | 1 | £5.25 | £5.25 | £5.25 | - | - | 3 | 3 | COtS | 3DJake | Link (https://www.3djake.uk/bigtreetech/stepper-motor-driver?sai=9877) | Invoice 12
 | 20 | E0005 | 1 | MicroSD card | 1 | £5.39 | £5.39 | £5.39 | - | - | 0.25 | 0.25 | COtS | CPC Farnell | Link (https://cpc.farnell.com/integral/inmsdh16g-100v10/16gb-microsdhc-v10-uhs-i-u1/dp/MD01157?st=micro%20sd%20card) | Invoice 6
 | 21 | E0006 | 2 | Microswitch | 1 | £0.35 | £0.35 | £0.35 | - | - | 3 | 3 | COtS | Amazon UK | Link (https://www.amazon.co.uk/dp/B08734MSDD?psc=1&ref=ppx_yo2ov_dt_b_product_details) | Invoice 8
 | 22 | E0007 | 1 | 8x Battery holder | 1 | £0.98 | £0.98 | £0.98 | - | - | 16 | 16 | COtS | CPC Farnell | Link (https://cpc.farnell.com/pro-power/pp002048/battery-holder-8x-aa-long-snap/dp/BT06499) | Invoice 6
 | 23 | E0008 | 1 | Snap-on battery connector | 1 | £0.23 | £0.23 | £0.23 | - | - | 20 | 20 | COtS | CPC Farnell | Link (https://cpc.farnell.com/pro-power/pp002032/battery-snaps-side-entry-safety/dp/BT06483?st=clip%20on%20connector) | Invoice 6
 | 24 | E0009 | 1 | Micro USB adapter | 1 | £0.77 | £0.77 | £0.77 | - | - | 13 | 13 | COtS | CPC Farnell | Link (https://cpc.farnell.com/raspberry-pi/sc0006/rpi-zero-v2-otg-adapter/dp/SC19068?st=otg) | Invoice 6
 | 25 | E0010 | 1 | Micro USB Cable | 1 | £0.96 | £0.96 | £0.96 | - | - | 8 | 8 | Cut to size | RS components | Link (https://uk.rs-online.com/web/p/bbc-micro-bit-add-ons/2260167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) | Invoice 4
 | 26 | E0011 | 1 | DC-DC buck converter | 1 | £1.40 | £1.40 | £1.40 | - | - | 12 | 12 | COtS | Amazon UK | Link (https://www.amazon.co.uk/Yizhet-Efficiency-Regulator-Converter-Adjustable/dp/B0823P6PW6) | Invoice 1
 | 27 | E0012 | 1 | Header pin, 1 row, 20 way | 2 | £0.10 | £0.20 | £0.00 | - | - | 0.6 | 1.2 | COtS | CPC Farnell | Link (https://cpc.farnell.com/multicomp/mc34739/header-1-row-vert-20way/dp/CN14497?st=headers%2020%20way) | Invoice 5
 | 28 | E0013 | 2 | SPDT Switch | 1 | £0.35 | £0.35 | £0.35 | - | - | 5 | 5 | COtS | Amazon UK | Link (https://www.amazon.co.uk/dp/B0B56S4F1X?psc=1&ref=ppx_yo2ov_dt_b_product_details) | Invoice 9
 | 29 | E0014 | 1 | AA Battery | 8 | £0.70 | £5.60 | £5.60 | - | - | 24 | 192 | COtS | Amazon UK | Link (https://www.amazon.co.uk/Duracell-Plus-Alkaline-Batteries-MN1500/dp/B093CC7XJQ?hvadid=534886019997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) | -
 | 30 | E0015 | 1 | 100uF capacitor | 1 | £0.12 | £0.12 | £0.00 | - | - | 1 | 1 | COtS | CPC Farnell | Link (https://cpc.farnell.com/multicomp/mcglr35v107m8x11/capacitor-100uf-35v-radial-105/dp/CA08278) | Invoice 10
 | 31 | E0016 | 1 | Breadboard | 1 | £0.90 | £0.90 | £0.90 | - | - | 33 | 33 | COtS | CPC Farnell | Link (https://cpc.farnell.com/pro-signal/psg-bb-400/breadboard-400-pin-white/dp/PC01770) | Invoice 10
 | 32 | E0017 | 1 | 6.3A fuse | 1 | £0.14 | £0.14 | £0.00 | - | - | 0.81 | 0.81 | COtS | CPC Farnell | Link (https://cpc.farnell.com/multicomp/mc000887/fuse-5x20mm-glass-quick-blow-6/dp/FF03079) | Invoice 10
 | 33 | E0018 | 1 | Buttons | 2 | £0.04 | £0.08 | £0.00 |  |  | 0.3 | 0.6 | COtS | Amazon UK | Link (https://www.amazon.co.uk/Youmile-100PACK-6x6x4-5mm-Momentary-Tactile/dp/B07XWY2NBK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) | -
 | 34 | E0019 | 1 | In-line fuse holder | 1 | £0.60 | £0.60 | £0.60 | - | - | 4.5 | 4.5 | COtS | CPC Farnell | Link (https://cpc.farnell.com/multicomp/mc11wf031/fuse-holder-in-line-5x20mm/dp/FF03278) | Invoice 10
 | 35 | E0020 | 1 | Jumper wire | 25 | £0.06 | £1.46 | £0.00 | - | - | 0.66 | 16.5 | COtS | Amazon UK | Link (https://www.amazon.co.uk/dp/B01EV70C78?psc=1&ref=ppx_yo2ov_dt_b_product_details) | Invoice 10
 | 36 | E0021 | 1 | Ultrasonic distance sensor | 1 | £2.52 | £2.52 | £2.52 | - | - | 8 | 8 | COtS | RS components | Link (https://uk.rs-online.com/web/p/bbc-micro-bit-add-ons/2153181?gb=s) | Invoice 4
 | Electronics IMechE BoM - Partial (£) |  |  |  |  |  |  | £62.17
Fixings, Fasteners, and other consumeables | 37 | CF0001 | 1 | Heatshrink | 20 | £0.02 | £0.38 | £0.00 | EVA | - | 5 | 5 | Cut to size | Amazon UK | Link (https://www.amazon.co.uk/ASHINER-Heat-Shrink-Tubing-User-Friendly-Multicolored/dp/B08XXGNJHG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) | -
 | 38 | CF0002 | 1 | Lead-free solder | 2 | £0.17 | £0.34 | £0.00 | - | - | 2 | 2 | Cut to size | RS Components | Link (https://uk.rs-online.com/web/p/solder/2441549?matchtype=&gad_source=1&gclsrc=aw.ds) | -
 |  | CF0003 | 1 | Stranded-core wire | 500 | 0.0002368421053 | £0.12 | £0.00 | - | - | 8 | 8 | Cut to size | Pi Hut UK | Link (https://thepihut.com/products/hook-up-wire-spool-set-22awg-stranded-core-10-x-25ft) | -
 | 39 | CF0004 | 1 | Solid-core wire | 500 | 0.0002631578947 | £0.13 | £0.00 | - | - | 8 | 8 | Cut to size | Pi Hut UK | Link (https://thepihut.com/products/prototyping-wire-spool-set) | -
 | 40 | CF0005 | 1 | Super glue | 1 | £0.72 | £0.72 | £0.72 | - | - | 1 | 1 | CotS | Amazon UK | Link (https://www.amazon.co.uk/Gorilla-4044205-Superglue-15g/dp/B003CT4XT0?s=industrial) | -
 | 41 | CF0006 | 2 | Velcro tape | 150 | 0.002596 | £0.39 | £0.39 | - | - | 8 | 8 | Cut to size | Amazon UK | Link (https://www.amazon.co.uk/VELCRO-Brand-Fasteners-Perfect-Office/dp/B0013D8IUC?hvadid=214440742293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) | -
 | 42 | CF0007 | 1 | M3x6 | 2 | £0.01 | £0.03 | £0.00 | Stainless Steel | 8000 | 0.36 | 0.72 | COtS | Amazon UK | Link (https://www.amazon.co.uk/dp/B0BR4WQP4R?psc=1&ref=ppx_yo2ov_dt_b_product_details) | Invoice 8
 | 43 | CF0008 | 1 | M3x10 | 25 | £0.01 | £0.33 | £0.00 | Stainless Steel | 8000 | 0.5 | 12.5 | COtS | Amazon UK | Link (https://www.amazon.co.uk/dp/B0BR4WQP4R?psc=1&ref=ppx_yo2ov_dt_b_product_details) | Invoice 8
 | 44 | CF0009 | 1 | M2.5x12 | 6 | £0.01 | £0.08 | £0.00 | Stainless Steel | 8000 | 0.4 | 2.4 | COtS | Amazon UK | Link (https://www.amazon.co.uk/dp/B0BR4WQP4R?psc=1&ref=ppx_yo2ov_dt_b_product_details) | Invoice 8
 |  | CF0010 |  | M2x10 | 2 | £0.01 | £0.03 | £0.00 | Stainless Steel | 8000 | 0.22 | 0.44 | COtS | Amazon UK | Link (https://www.amazon.co.uk/dp/B0BR4WQP4R?psc=1&ref=ppx_yo2ov_dt_b_product_details) | Invoice 8
 | 45 | CF0011 | 1 | Electrical tape | 400 | 3.333333333e-05 | £0.01 | £0.00 | PVC | - |  |  | Cut to size | Screwfix | Link (https://www.screwfix.com/p/ced-insulation-tape-black-33m-x-19mm/122pm) | -
 | Consumables IMechE BoM - Partial (£) |  |  |  |  |  |  | £1.11 | Total Mass (g) |  |  | 723.28
 | Notes:
 | Unit costs that are too small are denoted in scientific form (ie 4.06E-6) and are still in the unit £
 | Quantity is in units, except for those which are laser cut (mm2), those which are 3D printed (g), or tape/cut (mm)
 | Access invoices here | Back up link: | https://uoe-my.sharepoint.com/:f:/g/personal/s2289738_ed_ac_uk/EtWzKMgK9zBFi7NRyLfgglQBb7IdocdMV8jteqt58a28lA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

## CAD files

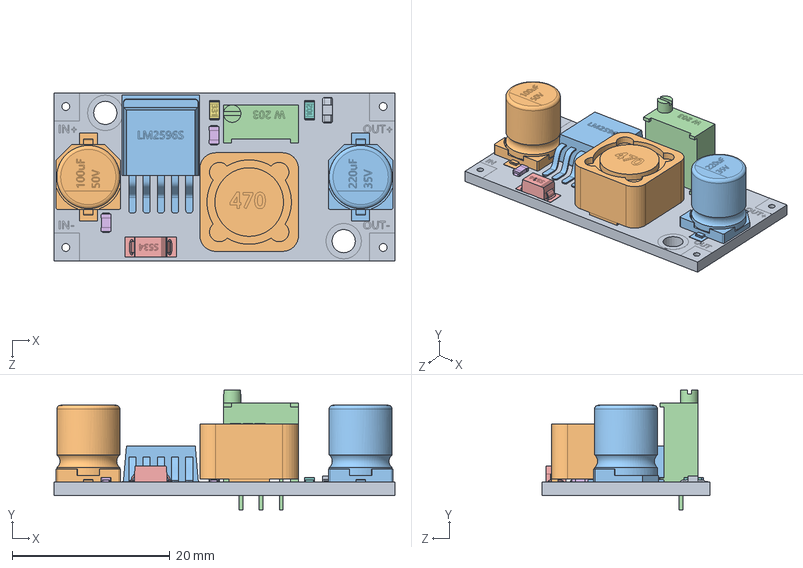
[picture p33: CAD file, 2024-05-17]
CAD files/LM2596 DC to DC Buck Converter/converterLM2596.SLDASM
43.2 x 15.1 x 21.2 mm
lm2596board
smd100uF
smd220uF
TrimmerW203
smdS537diode
smdceramiccapacitor x 2
smdResistor331
smdResistor102
smdLED
smbInductor470
LM2596S

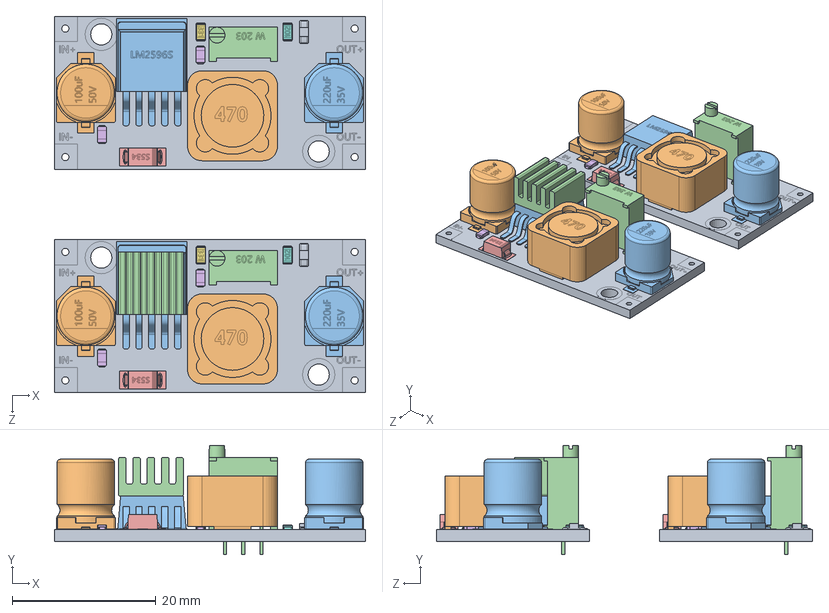
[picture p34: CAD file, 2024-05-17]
CAD files/LM2596 DC to DC Buck Converter/LM2596 with and without cooler.SLDASM
43.2 x 15.1 x 52.3 mm
lm2596board x 2
smd100uF x 2
smd220uF x 2
TrimmerW203 x 2
smdS537diode x 2
smdceramiccapacitor x 4
smdResistor331 x 2
smdResistor102 x 2
smdLED x 2
smbInductor470 x 2
LM2596S x 2
IC Cooler

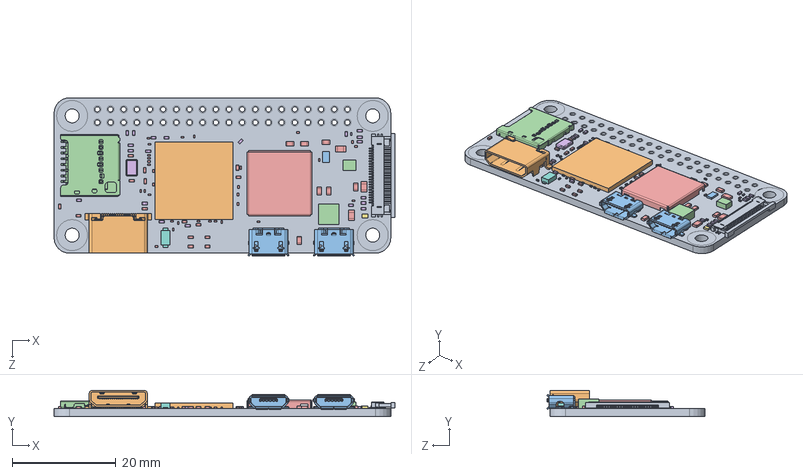
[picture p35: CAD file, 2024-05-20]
CAD files/Raspberry Pi Zero 2 W/Raspberry Pi Zero 2 W.SLDASM
65.8 x 5.05 x 30.6 mm
PCB, Raspberry Pi Zero 2 W
RP3A0-AU 2105 201221C, Raspberry Pi Zero 2 W
MicroUSB Port, Raspberry Pi Zero 2 W x 2
SD Card Slot, Raspberry Pi Zero 2 W
Wireless Module Cover, Raspberry Pi Zero 2 W
Crystal Resonator, Raspberry Pi Zero 2 W
LED, Raspberry Pi Zero 2 W
Diode, Schottky, Raspberry Pi Zero 2 W
54548-2271, 22 Pin FPC Connector, Raspberry Pi Zero 2 W
Mini HDMI Receptacle Port, Raspberry Pi Zero 2 W
RT8088AWSC, IC Reg Buck Prog 3A Sync 15WLCSP, Raspberry Pi Zero 2 W
SMD Inductor, Configurable, Raspberry Pi Zero 2 W x 2
SMD Capacitor, Configurable, Raspberry Pi Zero 2 W x 56
SMD Resistor, Configurable, Raspberry Pi Zero 2 W x 21

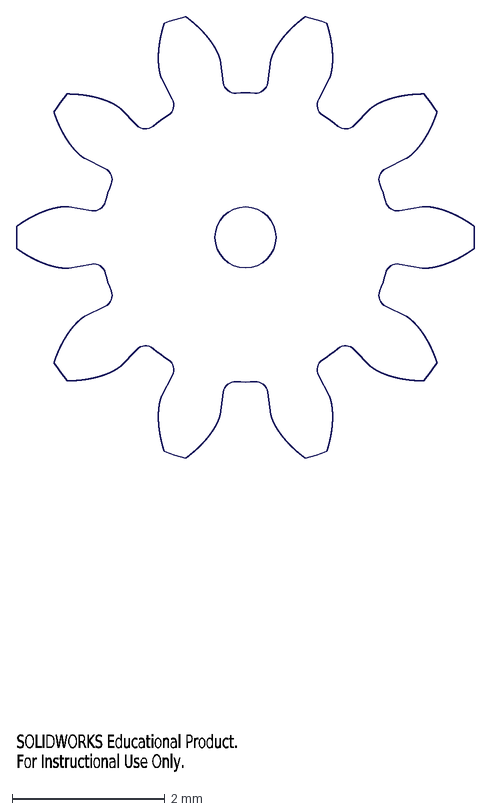
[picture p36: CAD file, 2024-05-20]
CAD files/Motor Gear/To Cut Main.DXF
SOLIDWORKS Educational Product.
For Instructional Use Only.

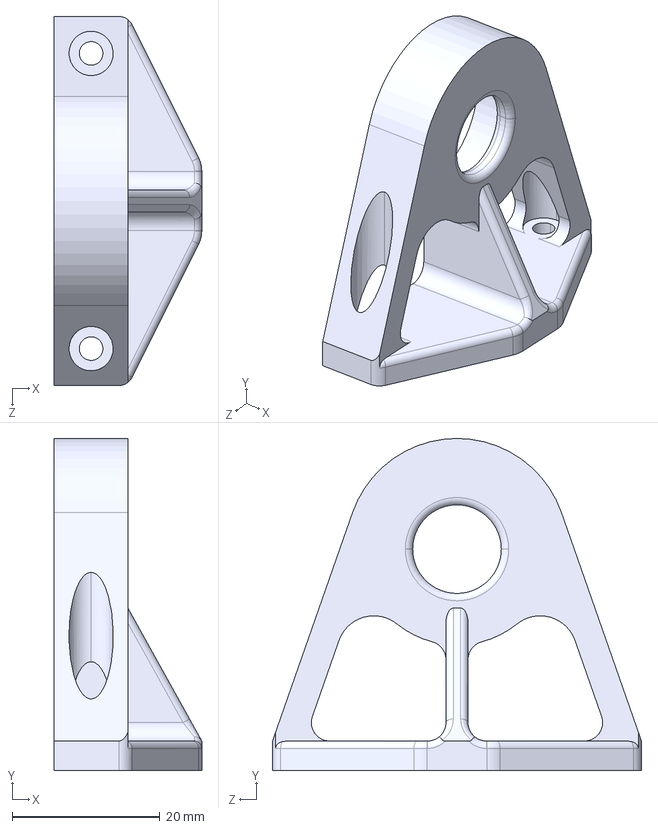
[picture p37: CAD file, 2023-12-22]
CAD files/Axle Holder/axle_holder_v01.STEP
20.0 x 45.0 x 50.0 mm

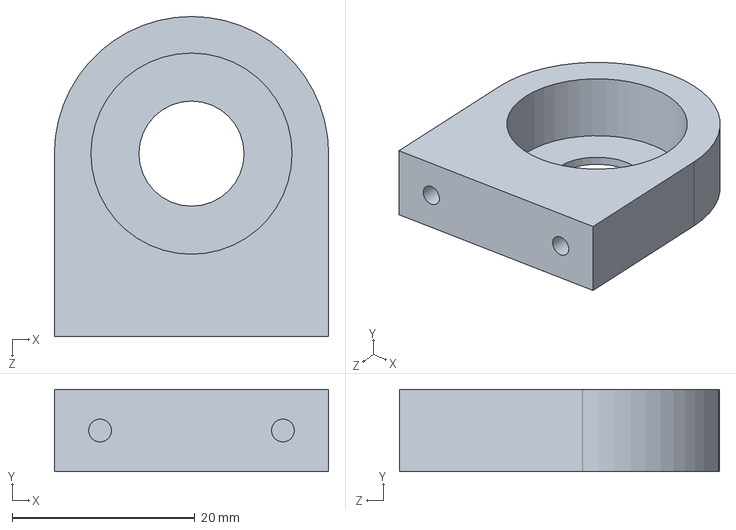
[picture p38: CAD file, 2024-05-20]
CAD files/Axle Holder/Bracket/Ball Bearing Bracket.SLDPRT
30.0 x 9.00 x 35.0 mm

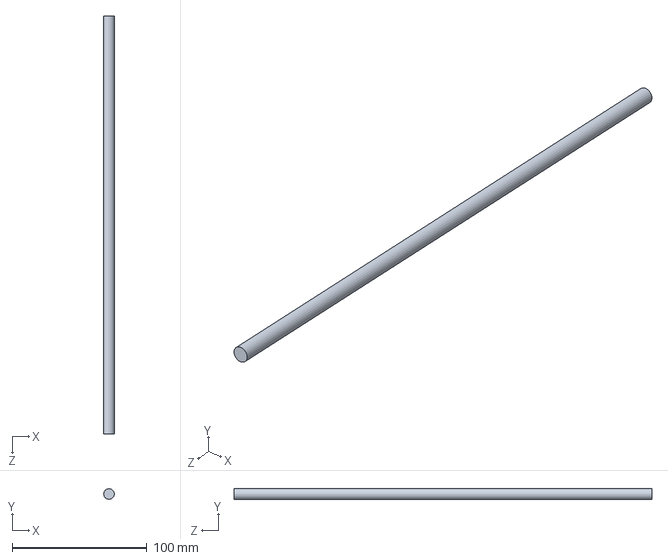
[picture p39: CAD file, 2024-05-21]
CAD files/Axle/Axle v03.SLDPRT
7.90 x 7.88 x 310.0 mm

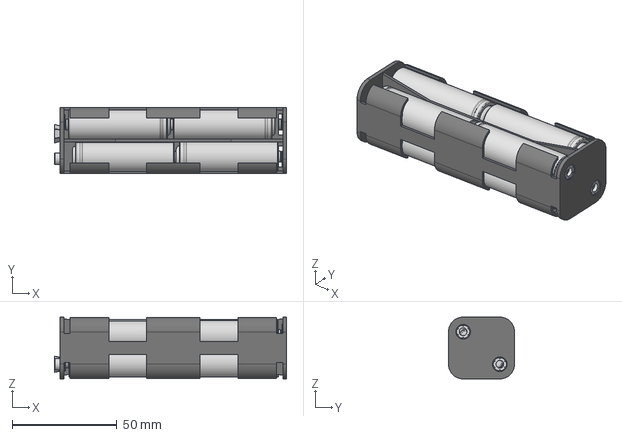
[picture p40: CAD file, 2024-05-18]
CAD files/Battery/Battery Pack v4.step
110.7 x 31.5 x 29.5 mm
AA Battery x 8
Battery Holder

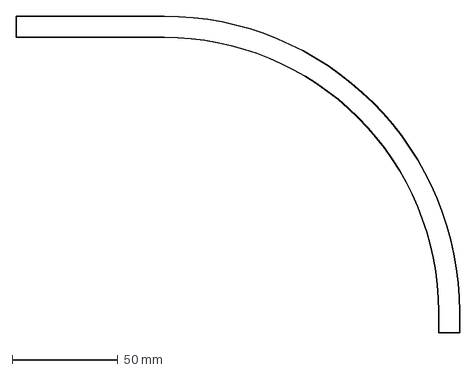
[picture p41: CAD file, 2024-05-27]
CAD files/Camera Holder/Camera Arm v03 in 2D.dxf
210.0 x 150.0 mm

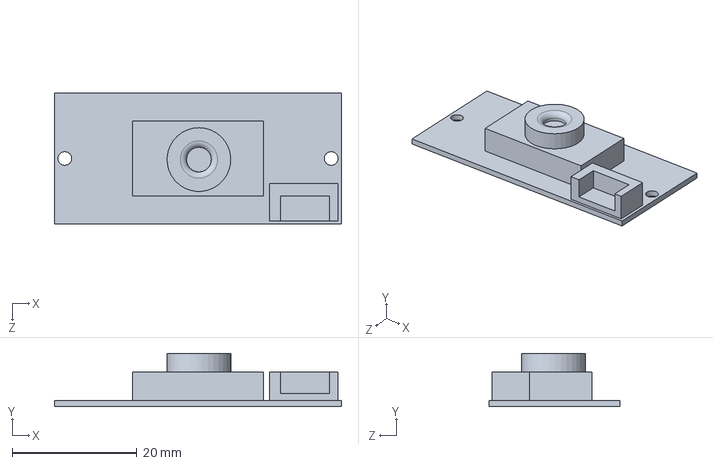
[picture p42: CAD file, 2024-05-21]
CAD files/Camera/Camera v01.SLDPRT
46.0 x 8.50 x 21.0 mm

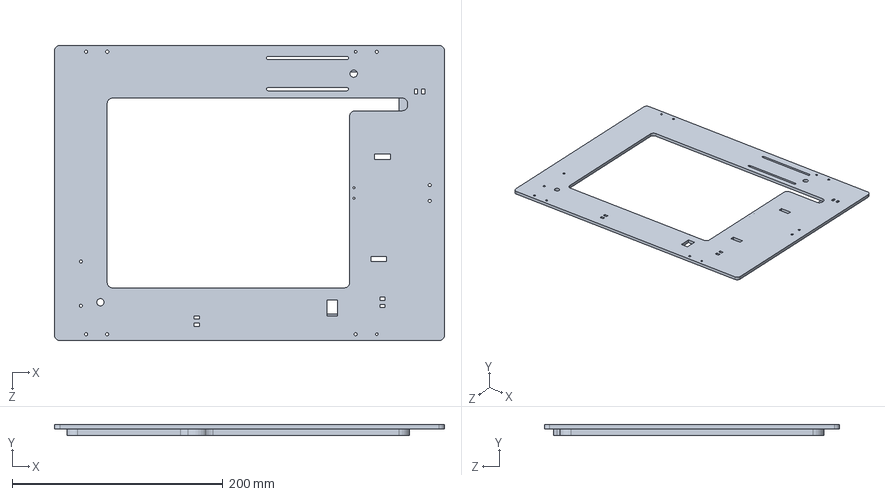
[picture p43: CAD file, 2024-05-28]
CAD files/Chassis/Chassis v08 skeleton.SLDPRT
370.0 x 10.0 x 280.0 mm

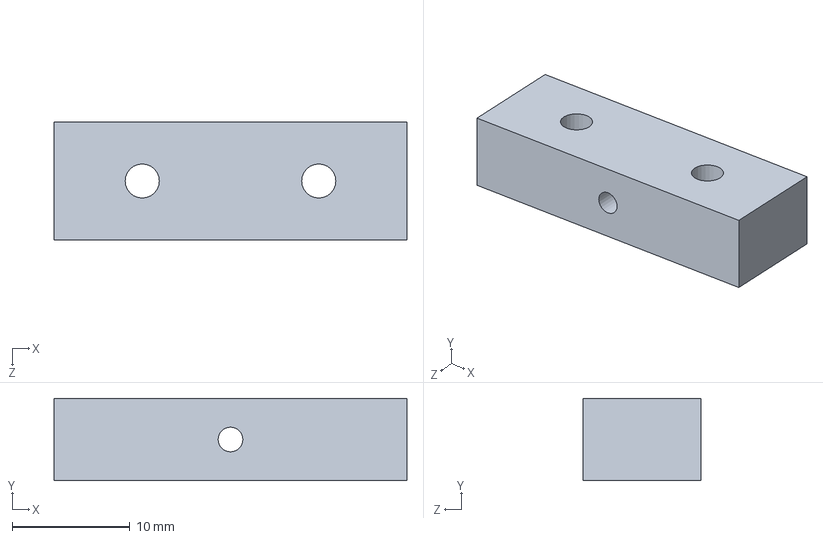
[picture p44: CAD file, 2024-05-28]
CAD files/Datum Holder/Datum Holder v03.SLDPRT
30.0 x 7.00 x 10.0 mm

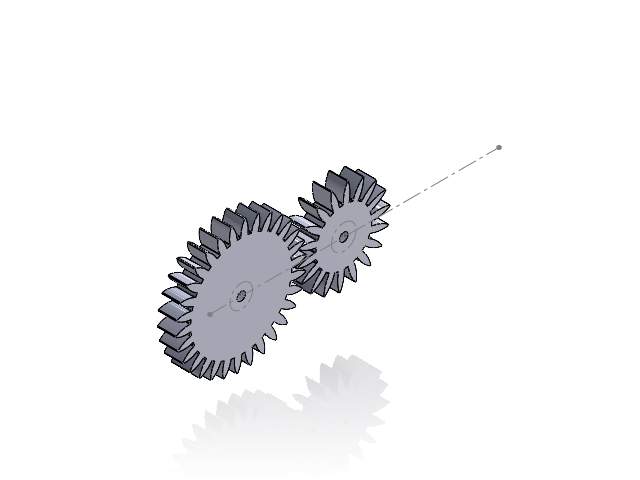
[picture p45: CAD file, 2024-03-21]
CAD files/Tests/Gear Testing.SLDASM
Middle Gear v01
Motor Gear v01

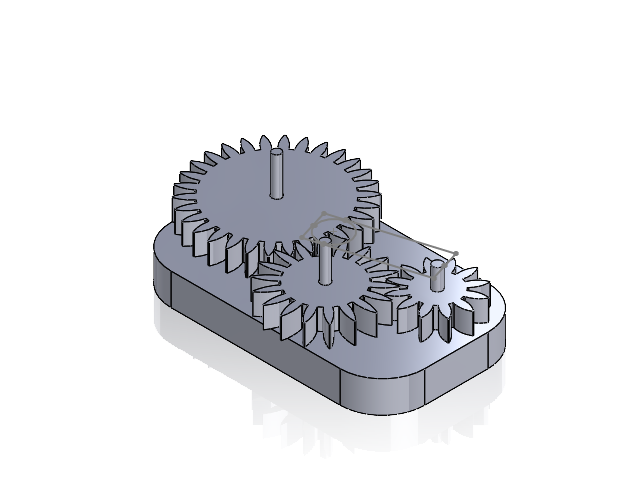
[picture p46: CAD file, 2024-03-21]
CAD files/Intermediate Gear/Assem1.SLDASM
Gear Holders
Gear with handle v01
Motor Gear v01
Middle Gear v01

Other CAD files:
CAD files/Axle/Assem1.SLDASM
CAD files/Motor Gear/To Cut Main v02.dwg
CAD files/Axle/Assem2.SLDASM
CAD files/Bracket/Ball Bearing Bracket.SLDPRT
CAD files/Axle Holder/axle_holder_v01.SLDPRT
CAD files/Axle/Axle female.SLDPRT
CAD files/Axle/Axle male.SLDPRT
CAD files/Axle/Axle v02.SLDPRT
CAD files/Axle/Axle without gear v01.SLDPRT
CAD files/Axle/Body1.SLDPRT
CAD files/Axle/Body2.SLDPRT
CAD files/Camera Holder/Bottom Bracket v01.SLDPRT
CAD files/Camera Holder/Camera Arm v02.SLDPRT
CAD files/Camera Holder/Camera Arm v03 IN 3D.SLDPRT
CAD files/Camera Holder/Camera Holder 1.SLDPRT
CAD files/Camera Holder/Camera Holder v01.SLDPRT
CAD files/Camera Holder/Camera Holder v02.SLDPRT
CAD files/Chassis/Chasses Flat.SLDPRT
CAD files/Chassis/Chassis v01 without alterations.SLDPRT
CAD files/Chassis/Chassis v02.SLDPRT
CAD files/Chassis/Chassis v03.SLDPRT
CAD files/Chassis/Chassis v04.SLDPRT
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

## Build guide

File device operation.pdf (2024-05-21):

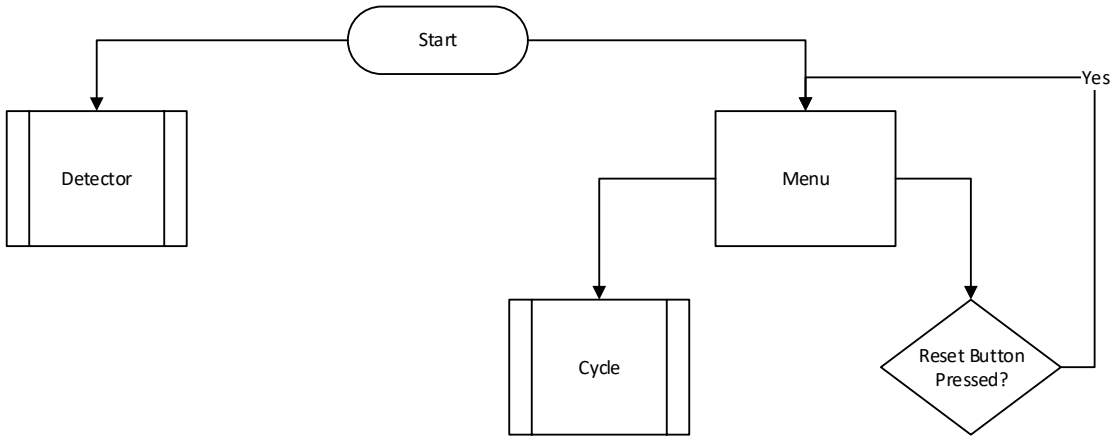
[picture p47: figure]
Start; Menu; Reset Button Pressed?; Yes; Cycle; Detector
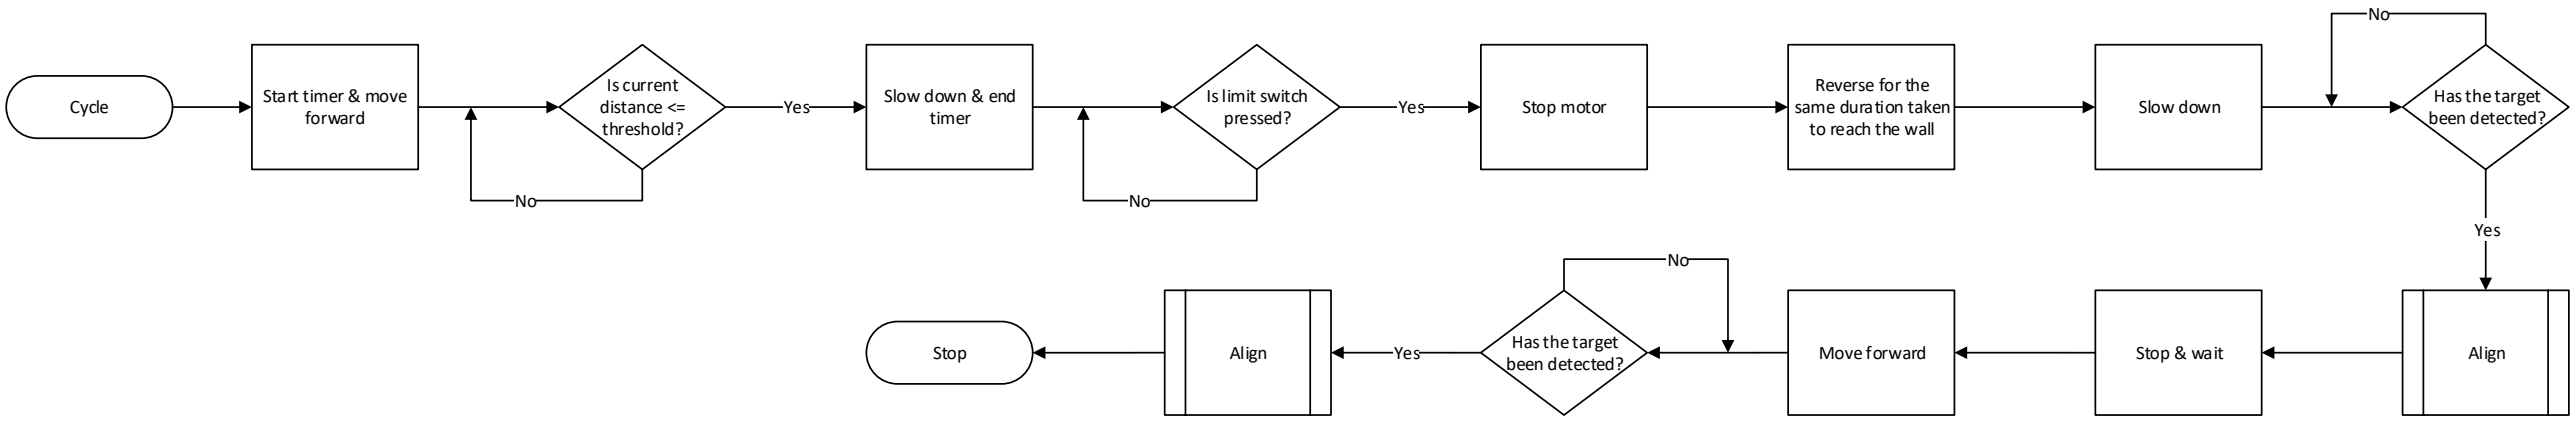
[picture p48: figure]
Cycle; Start timer & move; forward; Is current distance <= threshold?; Slow down & end timer; Is limit switch; pressed? Yes; Yes; Stop motor; Slow down; Has the target been detected?; Align; Move forward; Stop & wait Has the target; been detected? Stop; Reverse for the same duration taken to reach the wall
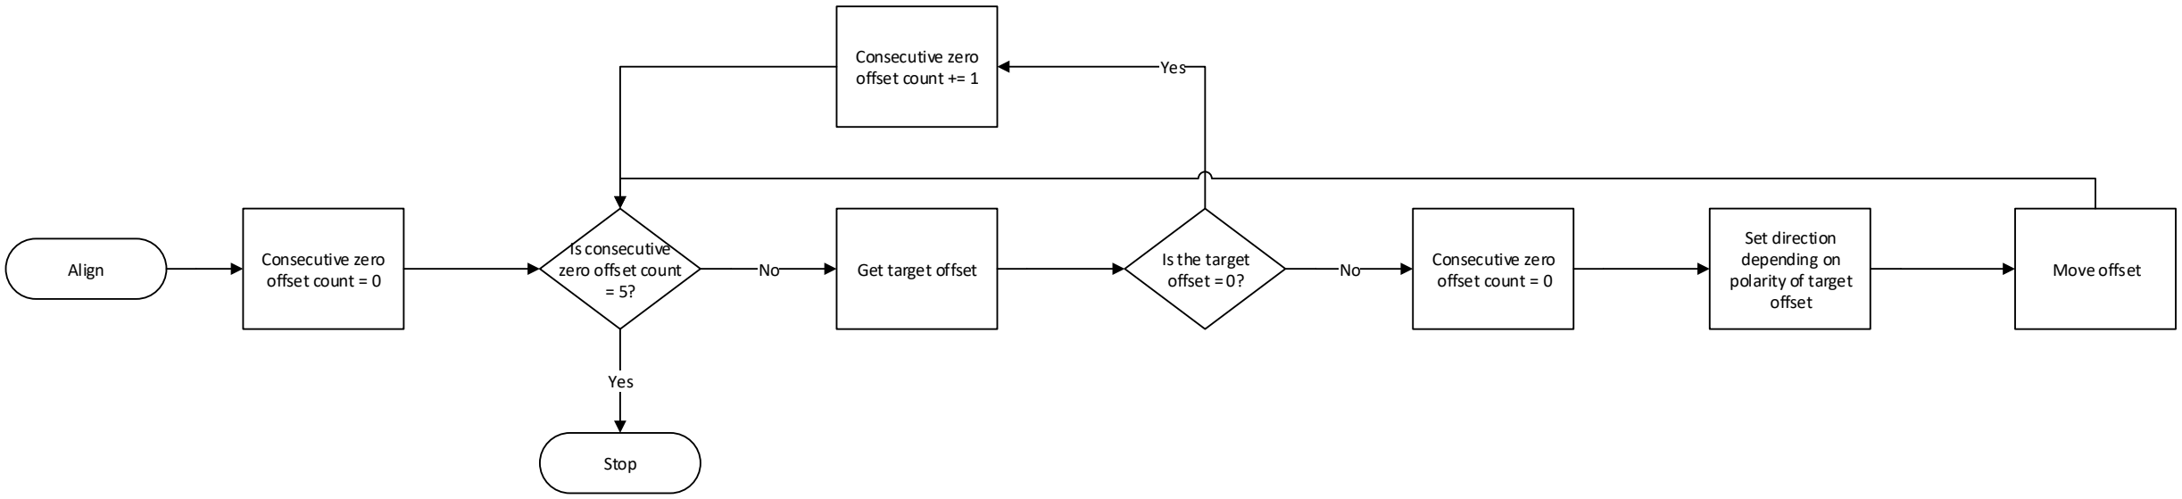
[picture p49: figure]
Align; Consecutive zero; offset count = 0; Is consecutive zero offset count = 5?; Get target offset; Is the target; offset = 0?; offset count += 1; Yes; Stop; Consecutive zero offset count = 0; Set direction depending on polarity of target offset; Move offset

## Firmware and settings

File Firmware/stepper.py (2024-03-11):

from machine import Pin
import utime

class Stepper:
    def __init__(self, step_pin, dir_pin, ms1_pin, ms2_pin, ms3_pin):
        self.step_pin = Pin(step_pin, Pin.OUT)
        self.dir_pin = Pin(dir_pin, Pin.OUT)
        self.position = 0

    def set_microstepping(self, resolution):
        if resolution not in [1, 2, 4, 8, 16]:
            raise ValueError("Invalid resolution. Must be one of [1, 2, 4, 8, 16]")
        settings = {
            1: (0, 0, 0),
            2: (1, 0, 0),
            4: (0, 1, 0),
            8: (1, 1, 0),
            16: (1, 1, 1)
        }
        for pin, value in zip(self.ms_pins, settings[resolution]):
            Pin(pin, Pin.OUT).value(value)
 
    def set_speed(self, speed, accelration):
        self.delay = 1 / abs(speed)  # delay in seconds
 
    def set_direction(self, direction):
        self.dir_pin.value(direction)
 
    def move_to(self, position):
        self.set_direction(1 if position > self.position else 0)
        while self.position != position:
            self.step_pin.value(1)
            utime.sleep(self.delay)
            self.step_pin.value(0)
            self.position += 1 if position > self.position else -1

    def move(self):
        pass

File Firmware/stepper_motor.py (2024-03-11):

from time import sleep
import pigpio

class StepperController:
    def __init__(self, dir_pin=20, step_pin=21):
        self.dir_pin = dir_pin
        self.step_pin = step_pin
        self.direction = 1 # 1 forward, 0 backward

        # Connect to pigpiod daemon
        pi = pigpio.pi()

        # Set up pins as an output
        pi.set_mode(dir_pin, pigpio.OUTPUT)
        pi.set_mode(step_pin, pigpio.OUTPUT)
    
    def set_pwm(self, duty_cycle, frequency):
        self.pi.set_PWM_dutycycle(self.step_pin, duty_cycle)
        self.pi.set_PWM_frequency(self.step_pin, frequency)

    def change_direction(self):
        self.direction = not self.direction
        self.pi.write(self.dir_pin, self.direction)

    def run(self, duration=10):
        start_time = sleep.time()
        try:
            while sleep.time() - start_time < duration:
                self.pi.write(self.dir_pin, self.direction)
                sleep(0.1)
        except KeyboardInterrupt:
            print("\nCtrl-C pressed. Stopping motor.")
        finally:
            self.stop()

    def stop(self):
        self.pi.set_PWM_dutycycle(self.step_pin, 0)  # Turn PWM off
        self.pi.stop()  # Disconnect from pigpiod

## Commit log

2023-12-01 :)
    Added folders for CAD files, electronics, and started on stepper motor controller class
2023-12-01 Stepper motor controller added
2023-12-02 Create Chassis v01 without alterations.SLDPRT
    [Chassis v01 without alterations.SLDPRT]
2023-12-04 Updates to CAD designs
    [Chassis v01 without alterations.SLDPRT, Wheels v01.SLDPRT, Wheels v02.SLDPRT]
2023-12-05 Updates + Chassis v02
    [Chassis v01 without alterations.SLDPRT, Chassis v02.SLDPRT, Wheels v02.SLDPRT]
2023-12-05 Create Chassis v03.SLDPRT
    New chassis has a gap for the gear and a platform to indicate where the battery pack should be
    [Chassis v03.SLDPRT]
2023-12-07 Many additional CAD files
    [Axle without gear v01.SLDPRT, Gear Testing.SLDASM, Middle Gear v01.SLDPRT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]
2023-12-08 CAD Updates
    Files updated to match new 8mm axle
    [Axle without gear v01.SLDPRT, Wheels v02.SLDPRT]
2023-12-08 Create wheel test 2 v3.step
    [wheel test 2 v3.step]
2023-12-08 Added Wheel v03
    [Wheels v03.step]
2023-12-12 Added wheel v04
    Reduced material use. 3d printed mass of wheel is 4.2g.
    [wheel_3s_v04.SLDPRT, wheel_wo_spokes_v04.SLDPRT]
2023-12-15 Added axle holder v01
    [axle_holder_v01.SLDPRT, axle_holder_v01.STEP, wheel_3s_v04.STEP]
2023-12-22 Update stepper_motor.py
    Changed the stepper motor controller to work with new firmware
2023-12-23 Update stepper_motor.py
    Added error handling and acceleration functionality
    [stepper_motor.py]
2023-12-23 Update stepper_motor.py
    Added step counter
2023-12-23 Update target_detector.py
    Added error handling
    [target_detector.py]
2023-12-23 Added schematic
    [schematic v01.fzz]
2024-01-19 Debugging Motor Controller & Usage
2024-03-10 testing motor
2024-03-11 Implementing new motor control technique
    Using PIGPIO to produce PWM signals. This uses through hardware rather than software like previously.
2024-03-17 debugging
    fixing continuous y displacement output
    [firmwareV3.py, target_detector_v2.py]
2024-03-20 Create schematic v02.fzz
    [schematic v02.fzz]
2024-03-20 A ton of updates to CAD files
    [Assem1.SLDASM, Assem2.SLDASM, Axle female.SLDPRT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]
2024-03-21 Organising files
    [schematic v02.fzz]
2024-03-21 Added wiring diagram
    [schematic v02.fzz]
2024-03-24 Create motor mount v2.step
    [motor mount v2.step]
2024-03-24 Update schematic v02.fzz
    [schematic v02.fzz]
2024-04-25 Update main_test.py
    Using asyncio instead of threading due to having issues with target detector not running with the main program + other improvements. Needs testing
    [main_test.py]
2024-05-17 Adding updated circuit diagrams
    [circuit diagram v03.fzz]
2024-05-17 Adding CAD models
    [20x2_Male_Pin_Header.STEP, 54548-2271, 22 Pin FPC Connector, Raspberry Pi Zero 2 W.SLDPRT, Crystal Resonator, Raspberry Pi Zero 2 W.SLDPRT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]
2024-05-18 Sensor I/O testing
2024-05-18 adding gpio pin
2024-05-19 updates lol
    [Axle gear.3mf, Axle gear.f3d, Axle v02.SLDPRT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]
2024-05-19 Shortening filenames
    [22 Pin FPC Connector.SLDPRT, Crystal Resonator.SLDPRT, Diode.SLDPRT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]
2024-05-19 Create Motor Mount v4.step
    [Motor Mount v4.step]
2024-05-19 big CAD updates
    [ASSEMBLY v01.SLDASM, Ball Bearing Bracket.SLDPRT, Chassis v07 IN 3D.SLDPRT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]
2024-05-19 Updates, updates, updates
    [5972K501_Ball Bearing.SLDPRT, Bigger Gear.SLDPRT, Camera Holder v03 IN 3D.SLDPRT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]
2024-05-19 Added RPi and buck converter
2024-05-19 Adding circuit diagram
    [circuit diagram v4.fzz]
2024-05-19 Create 4 male header pin v2.step
    [4 male header pin v2.step]
2024-05-19 Assembly halfway done
    [54548-2271, 22 Pin FPC Connector, Raspberry Pi Zero 2 W.SLDPRT, Crystal Resonator, Raspberry Pi Zero 2 W.SLDPRT, Diode, Schottky, Raspberry Pi Zero 2 W.SLDPRT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]
2024-05-19 Update circuit diagram v4.fzz
    [circuit diagram v4.fzz]
2024-05-19 i hate myself
    [Ball Bearing Bracket.SLDPRT, Camera Holder 1.SLDPRT, Chassis v07 IN 3D.SLDPRT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]
2024-05-20 Create Datum v2.step
    [Datum v2.step]
2024-05-20 Harry where are you
    [Camera Arm v03 IN 3D.SLDPRT, Camera Holder v02.SLDPRT, Chassis v07 IN 3D.SLDPRT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]
2024-05-20 Create ultrasonic sensor holder v4.step
    [ultrasonic sensor holder v4.step]
2024-05-20 First finalised edition of assembly
    [Chassis v07 IN 3D.SLDPRT, Datum v2.SLDPRT, ultrasonic sensor holder v4.step.SLDPRT]
2024-05-20 Create Power Switch Assem v3.step
    [Power Switch Assem v3.step]
2024-05-20 Correcting diagram
    [circuit diagram v4.fzz]
2024-05-21 ASSEMBLY FINAL WOOOO
    [Axle v03.SLDPRT, Ball Bearing Bracket.SLDPRT, Bigger Gear.SLDPRT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]
2024-05-21 almost there
    [Ball Bearing Bracket.SLDPRT, Bottom Bracket v01.SLDPRT, Camera Holder v02.SLDPRT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]
2024-05-21 Create device operation.pdf
2024-05-22 BoM versions and README
    [BoM SUBMISSION.xlsx]
2024-05-28 Second last push!!!
    [Chassis v08 skeleton.SLDPRT, Stand v01.SLDPRT]
2024-05-28 The final push :)
    [BoM.xlsx]
